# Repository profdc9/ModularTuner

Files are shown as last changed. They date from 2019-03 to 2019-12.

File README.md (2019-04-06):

This a project to create a Modular Antenna Tuner System that can be reconfigured for
different needs.  This material is copyrighted by Daniel Marks (KW4TI) and licensed under
the Creative Commons License CC-BY-SA 4.0.

This project is a toolkit for making automatic antenna tuners and smart HF antennas.

A description and documentation of this project may be found in the "doc" directory as
ModularTuner-Guide.pdf.

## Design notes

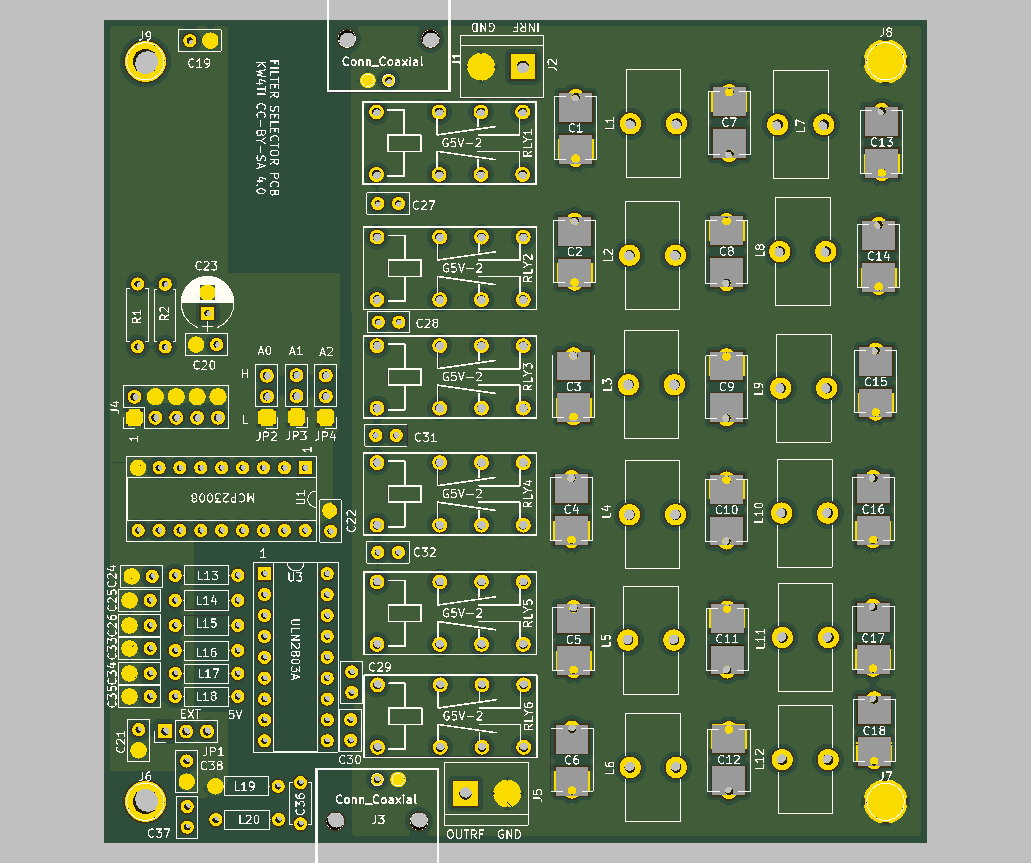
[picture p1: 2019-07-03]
Tuner/Filter/Filter.png

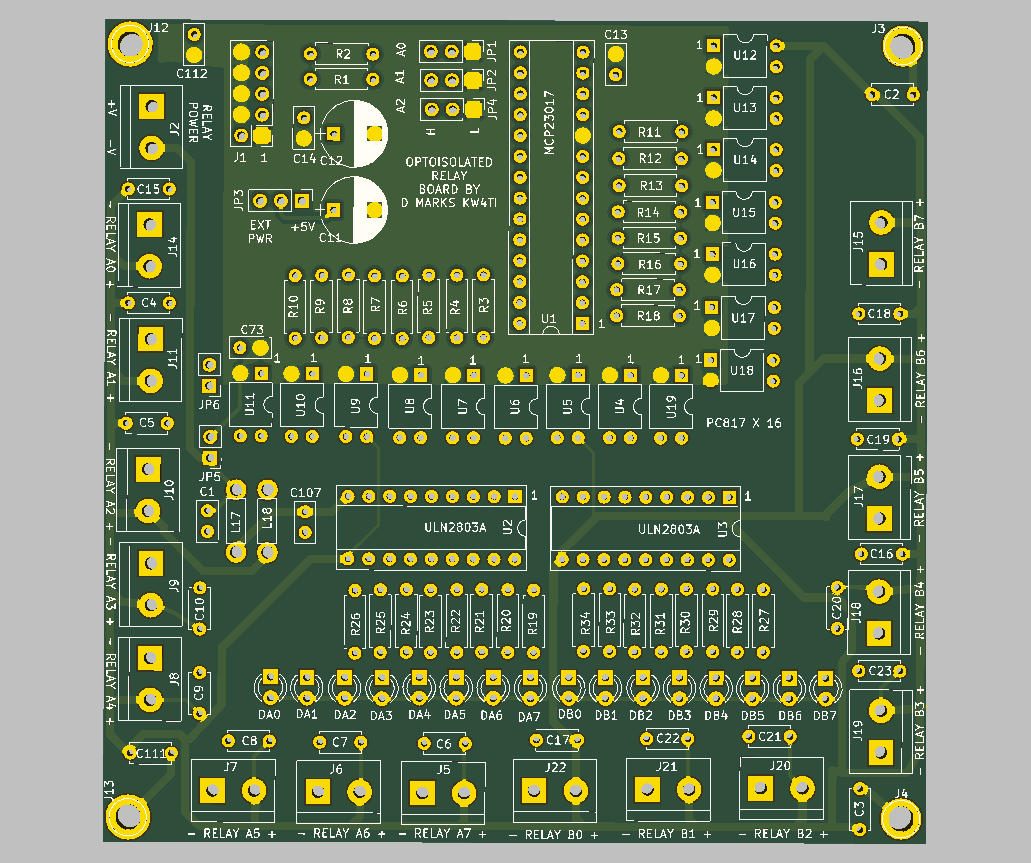
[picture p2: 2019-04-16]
Tuner/OptoisolatedRelay/OptoisolatedRelay.png

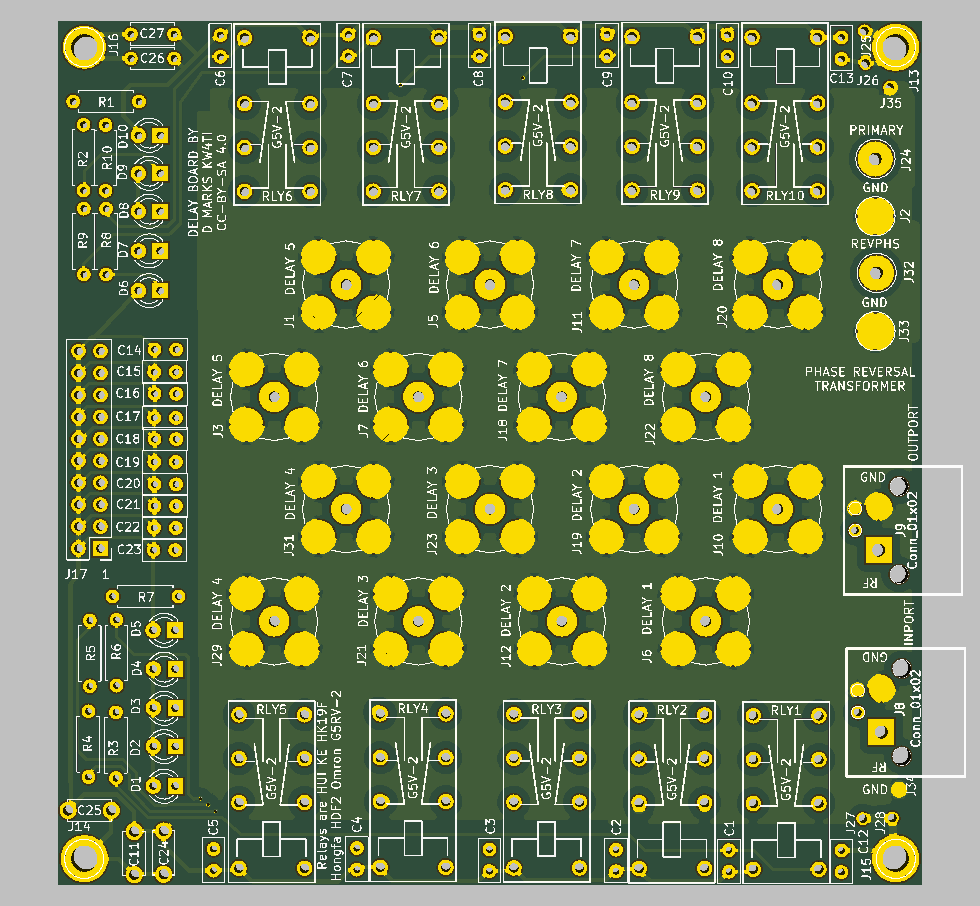
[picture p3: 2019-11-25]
Tuner/DelayLine/DelayLine.png

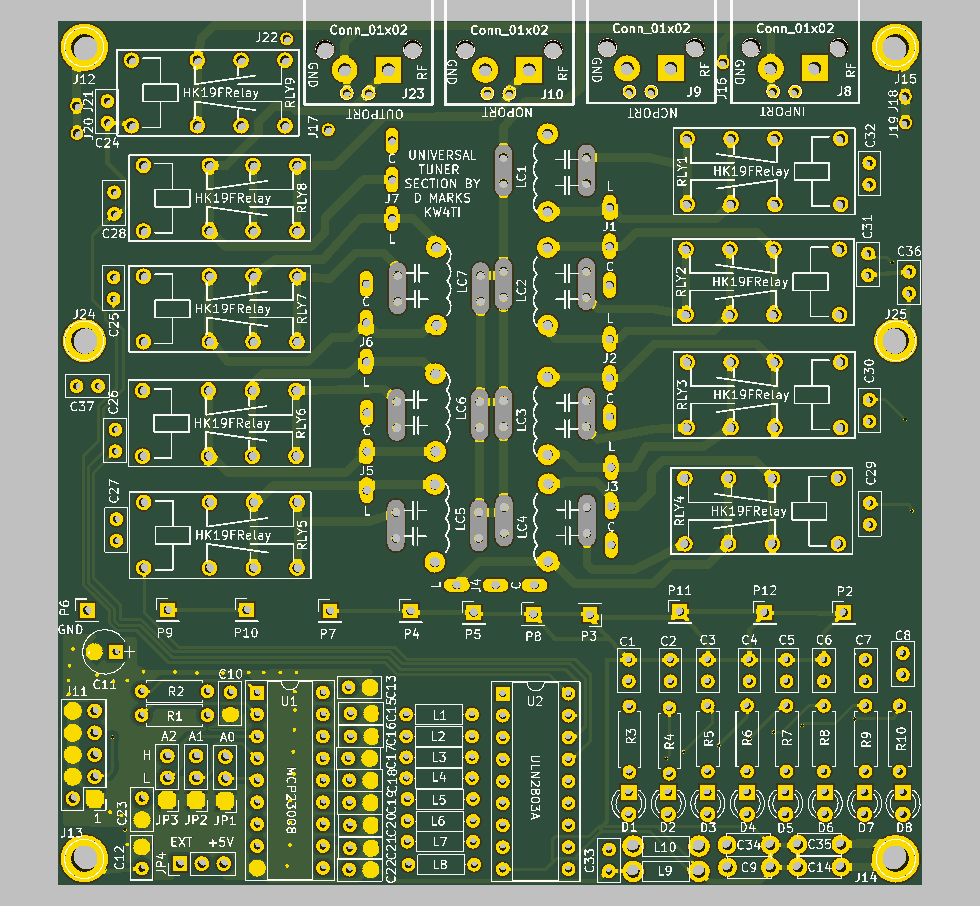
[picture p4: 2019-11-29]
Tuner/ReversibleLittleSection/ReversibleSection.png

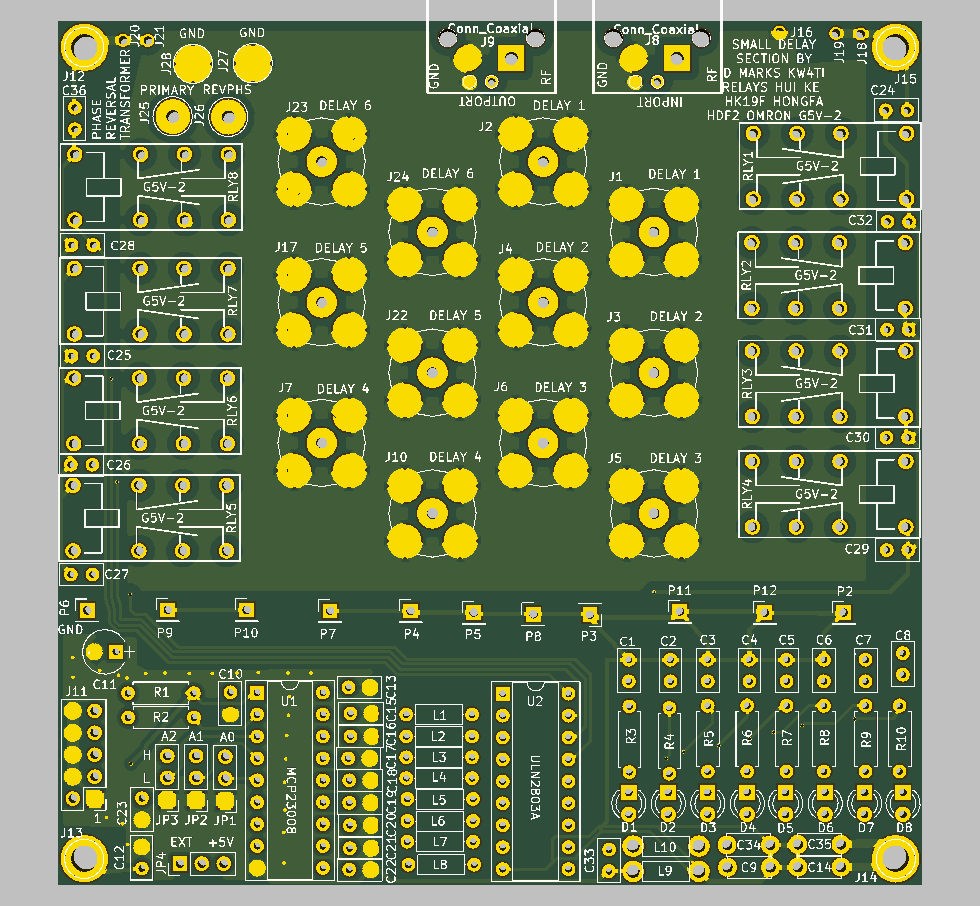
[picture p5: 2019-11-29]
Tuner/LittleDelayLine/LittleDelayLine.png

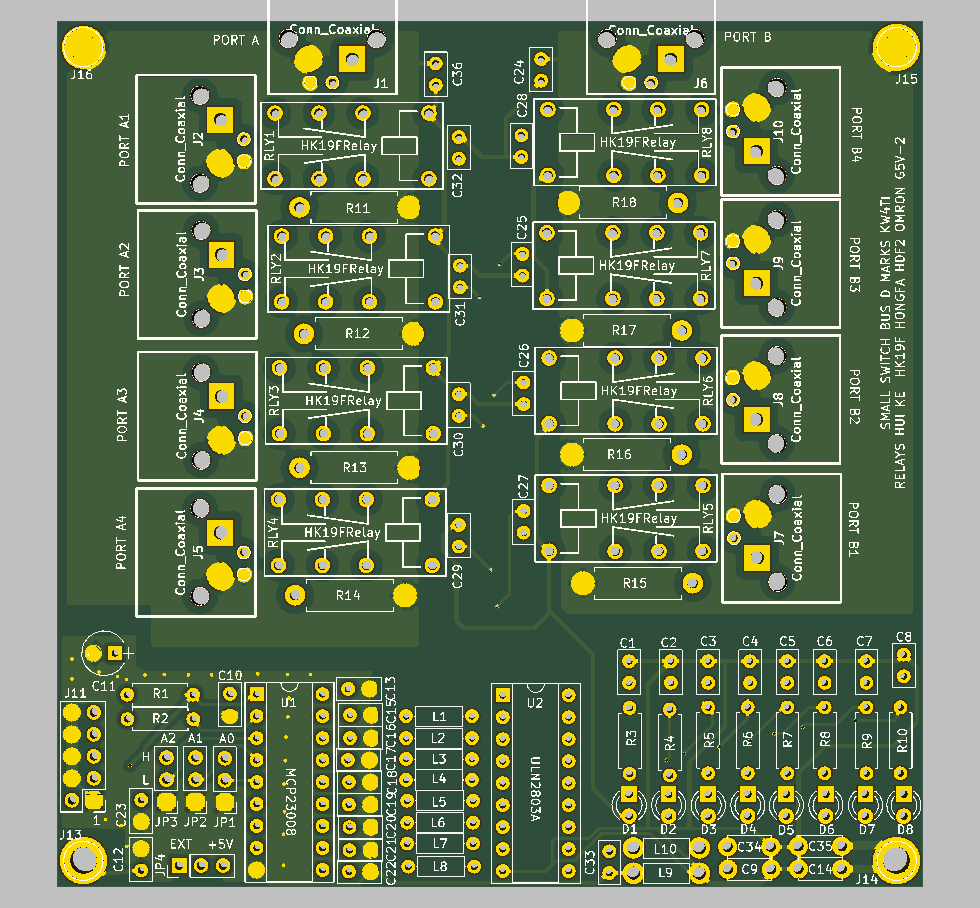
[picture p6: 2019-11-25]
Tuner/LittleSwitchBus/LittleSwitchBus.png

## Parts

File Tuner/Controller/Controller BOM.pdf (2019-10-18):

Controller

Controller Bill Of Materials

Ref | Value
C1 | 100 nF 50 V ceramic disc capacitor
C2 | 100 nF 50 V ceramic disc capacitor
C3 | 100 nF 50 V ceramic disc capacitor
C4 | 1000 uF 10 V electrolytic polarized capacitor
C5 | 100 nF 50 V ceramic disc capacitor
C6 | 100 uF 25 V electrolytic polarized capacitor
C7 | 100 nF 50 V ceramic disc capacitor
C8 | 10 nF 50 V ceramic disc capacitor
C9 | 10 nF 50 V ceramic disc capacitor
C10 | 10 nF 50 V ceramic disc capacitor
C11 | 10 nF 50 V ceramic disc capacitor
C12 | 10 nF 50 V ceramic disc capacitor
C13 | 10 nF 50 V ceramic disc capacitor
C14 | 10 nF 50 V ceramic disc capacitor
C15 | 100 nF 50 V ceramic disc capacitor
C16 | 100 nF 50 V ceramic disc capacitor
C17 | 100 nF 50 V ceramic disc capacitor
C18 | 10 nF 50 V ceramic disc capacitor
C19 | 100 nF 50 V ceramic disc capacitor
C20 | 100 nF 50 V ceramic disc capacitor
C21 | 100 nF 50 V ceramic disc capacitor
C22 | 10 nF 50 V ceramic disc capacitor
C23 | 10 nF 50 V ceramic disc capacitor
C24 | 10 nF 50 V ceramic disc capacitor
C25 | 100 nF 50 V ceramic disc capacitor
C26 | 100 nF 50 V ceramic disc capacitor
C27 | 10 nF 50 V ceramic disc capacitor
C28 | NC
C29 | NC
C30 | 100 nF 50 V ceramic disc capacitor
C31 | 100 nF 50 V ceramic disc capacitor
C32 | 100 nF 50 V ceramic disc capacitor
C33 | 100 nF 50 V ceramic disc capacitor
C34 | 100 nF 50 V ceramic disc capacitor
C35 | 100 nF 50 V ceramic disc capacitor
C36 | 100 uF 25 V electrolytic polarized capacitor
C37 | 100 nF 50 V ceramic disc capacitor
C38 | 100 nF 50 V ceramic disc capacitor
C39 | 100 nF 50 V ceramic disc capacitor
C40 | 100 nF 50 V ceramic disc capacitor
C41 | 100 nF 50 V ceramic disc capacitor
C42 | 100 nF 50 V ceramic disc capacitor
C43 | 10 nF 50 V ceramic disc capacitor
C44 | 10 nF 50 V ceramic disc capacitor

C45 | 10 nF 50 V ceramic disc capacitor
C46 | 100 nF 50 V ceramic disc capacitor
D1 | 1N4004
D2 | 1N4004
D3 | 1N5711 or “ebay 1N60P”
D4 | 1N5711 or “ebay 1N60P”
D5 | 1N5711 or “ebay 1N60P”
D6 | 1N5711 or “ebay 1N60P”
D7 | 1N5711 or “ebay 1N60P”
D8 | 3 mm LED
D9 | 1N5711 or “ebay 1N60P”
D10 | 1N5711 or “ebay 1N60P”
D11 | 1N5711 or “ebay 1N60P”
D12 | 1N5819
D13 | 1N4148
D14 | 1N5819
D15 | 1N4148
D16 | 1N4148
D17 | 1N5711 or “ebay 1N60P”
D18 | 1N4148
D19 | 1N4148
D20 | 1N4148
D21 | 1N4729A
D24 | 1N5819
D25 | 1N5819
D27 | 1N4733A
D28 | 1N4733A
J1 | 2 rows of 5 pin headers 2.54 mm spacing
J2 | 2 rows of 5 pin headers 2.54 mm spacing
J3 | 2 rows of 5 pin headers 2.54 mm spacing
J4 | 2 rows of 5 pin headers 2.54 mm spacing
J5 | 2 rows of 5 pin headers 2.54 mm spacing
J6 | 2 position 5.08 mm screw terminal block
J7 | 2 rows of 5 pin headers 2.54 mm spacing
J8 | 1 rows of 6 pin headers 2.54 mm spacing
J9 | 2 position 5.08 mm screw terminal block or right-angle BNC isolated PCB receptacle
J10 | 1 rows of 5 pin headers 2.54 mm spacing
J11 | 2 position 5.08 mm screw terminal block or right-angle BNC isolated PCB receptacle
J13 | 2 position 5.08 mm screw terminal block or right-angle BNC isolated PCB receptacle
J15 | 2 position 5.08 mm screw terminal block
J16 | JST 2.54 mm male pin socket, 7 pins, 2.54 mm spacing
JP1 | 1 rows of 3 pin headers 2.54 mm spacing
Q1 | 2N3904
Q2 | 2N3904
Q3 | 2N3904
Q4 | 2N3904
Q5 | 2N3904
Q6 | 2N3904
Q7 | 2N3904

Page

3

Q8 | 2N3904
Q9 | 2N7000
Q10 | 2N7000
Q11 | 2N7000
Q12 | 2N7000
R1 | 10k ¼ watt resistor
R2 | 10k ¼ watt resistor
R3 | 1k ¼ watt resistor
R4 | 330R ¼ watt resistor
R5 | 470R ¼ watt resistor
R6 | 10k ¼ watt resistor
R7 | 51R ¼ watt resistor
R8 | 10k ¼ watt resistor
R9 | 10k ¼ watt resistor
R10 | 1k ¼ watt resistor
R11 | 330R ¼ watt resistor
R12 | 1k ¼ watt resistor
R13 | 330R ¼ watt resistor
R14 | 10k ¼ watt resistor
R15 | 1k ¼ watt resistor
R16 | NC
R17 | NC
R18 | 10k ¼ watt resistor
R19 | 100R ¼ watt resistor
R20 | 22k ¼ watt resistor
R21 | 220R ¼ watt resistor
R22 | 220R ¼ watt resistor
R23 | 51R ¼ watt resistor
R24 | 1k ¼ watt resistor
R25 | 1k ¼ watt resistor
R26 | 1k ¼ watt resistor
R27 | 51R ¼ watt resistor
R28 | 220R ¼ watt resistor
R29 | 1k ¼ watt resistor
R30 | 1k ¼ watt resistor
R31 | 1k ¼ watt resistor
R32 | 100R ¼ watt resistor
R33 | 1k ¼ watt resistor
R34 | NC
R35 | 10k ¼ watt resistor
R36 | 1k ¼ watt resistor
R37 | 1.5k ¼ watt resistor
R38 | 1.5k ¼ watt resistor
R39 | 1k ¼ watt resistor
R40 | 1k ¼ watt resistor
R41 | 220R ¼ watt resistor
R42 | 100R ¼ watt resistor
R43 | 1.5k ¼ watt resistor
R44 | 1.5k ¼ watt resistor

R45 | 56R 1 watt resistor
R46 | 1k ¼ watt resistor
R47 | 22k ¼ watt resistor
R48 | 100R ¼ watt resistor
R49 | 220R ¼ watt resistor
R50 | short circuit wire
R51 | 22k ¼ watt resistor
R52 | 220R ¼ watt resistor
R53 | short circuit wire
R54 | 10k ¼ watt resistor
R55 | short circuit wire
R56 | 1k ¼ watt resistor
R57 | 1k ¼ watt resistor
R58 | 1k ¼ watt resistor
R59 | 1.5k ¼ watt resistor
R60 | 1.5k ¼ watt resistor
R61 | 1.5k ¼ watt resistor
R62 | 220R ¼ watt resistor
R63 | 10k ¼ watt resistor
R64 | 56R 1 watt
R65 | 56R 1 watt
R66 | 10k ¼ watt resistor
R67 | 10k ¼ watt resistor
R68 | 10k ¼ watt resistor
R69 | 10k ¼ watt resistor
R70 | 10k ¼ watt resistor
R71 | 10k ¼ watt resistor
R72 | 10k ¼ watt resistor
R73 | 10k ¼ watt resistor
U1 | 74HC393 DIP-14
U2 | 74HC14 DIP-14
U3 | 74HC86 DIP-14
U4 | LM350 TO-220
UB1 | BLUEPILL: solder two 20 pin header sockets into board
| and 20 pin headers on Bluepill, slot into the sockets.

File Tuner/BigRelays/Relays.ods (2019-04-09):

 | E:/ModularTuner/Tuner/BigRelays/Relays.sch
Ref | Value
C1 | 10 nF 50 V ceramic disc capacitor
C2 | 10 nF 50 V ceramic disc capacitor
C3 | 10 nF 50 V ceramic disc capacitor
C4 | 10 nF 50 V ceramic disc capacitor
C5 | 10 nF 50 V ceramic disc capacitor
C6 | 10 nF 50 V ceramic disc capacitor
C7 | 10 nF 50 V ceramic disc capacitor
C8 | 10 nF 50 V ceramic disc capacitor
C9 | 10 nF 50 V ceramic disc capacitor
C10 | 10 nF 50 V ceramic disc capacitor
C11 | 2200 pF to 10 nF 630 V ceramic disc capacitor
C12 | 10 nF 50 V ceramic disc capacitor
C13 | 10 nF 50 V ceramic disc capacitor
C14 | 10 nF 50 V ceramic disc capacitor
C15 | 10 nF 50 V ceramic disc capacitor
C16 | 10 nF 50 V ceramic disc capacitor
C17 | 10 nF 50 V ceramic disc capacitor
C18 | 10 nF 50 V ceramic disc capacitor
C19 | 10 nF 50 V ceramic disc capacitor
C20 | 10 nF 50 V ceramic disc capacitor
C21 | 10 nF 50 V ceramic disc capacitor
C22 | 10 nF 50 V ceramic disc capacitor
C23 | 10 nF 50 V ceramic disc capacitor
C24 | 2200 pF to 10 nF 630 V ceramic disc capacitor
C25 | 2200 pF to 10 nF 630 V ceramic disc capacitor
D1 | 3 mm LED
D2 | 3 mm LED
D3 | 3 mm LED
D4 | 3 mm LED
D5 | 3 mm LED
D6 | 3 mm LED
D7 | 3 mm LED
D8 | 3 mm LED
D9 | 3 mm LED
D10 | 3 mm LED
J8 | 2 position 5.08 mm screw terminal block
J9 | 2 position 5.08 mm screw terminal block
J10 | 2 position 5.08 mm screw terminal block
J11 | 2 position 5.08 mm screw terminal block
J16 | 2 position 5.08 mm screw terminal block
J17 | 2 rows of 10 pin headers 2.54 mm spacing
J18 | 2 position 5.08 mm screw terminal block
J19 | 1 row of 3 pin header 2.54 mm spacing
LC1 | Capacitor or Inductor
LC2 | Capacitor or Inductor
LC3 | Capacitor or Inductor
LC4 | Capacitor or Inductor
LC5 | Capacitor or Inductor
LC6 | Capacitor or Inductor
LC7 | Capacitor or Inductor
LC8 | Capacitor or Inductor
R1 | 1k ¼ watt resistor
R2 | 1k ¼ watt resistor
R3 | 1k ¼ watt resistor
R4 | 1k ¼ watt resistor
R5 | 1k ¼ watt resistor
R6 | 1k ¼ watt resistor
R7 | 1k ¼ watt resistor
R8 | 1k ¼ watt resistor
R9 | 1k ¼ watt resistor
R10 | 1k ¼ watt resistor
RLY1 | “Big” Relay (see documentation)
RLY2 | “Big” Relay (see documentation)
RLY3 | “Big” Relay (see documentation)
RLY4 | “Big” Relay (see documentation)
RLY5 | “Big” Relay (see documentation)
RLY6 | “Big” Relay (see documentation)
RLY7 | “Big” Relay (see documentation)
RLY8 | “Big” Relay (see documentation)
RLY9 | “Big” Relay (see documentation)
RLY10 | “Big” Relay (see documentation)
RLY11 | “Big” Relay (see documentation)
RLY12 | “Big” Relay (see documentation)

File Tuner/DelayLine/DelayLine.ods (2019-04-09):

 | DelayLine Bill of Materials
Ref | Value
C1 | 10 nF 50 V ceramic disc capacitor
C2 | 10 nF 50 V ceramic disc capacitor
C3 | 10 nF 50 V ceramic disc capacitor
C4 | 10 nF 50 V ceramic disc capacitor
C5 | 10 nF 50 V ceramic disc capacitor
C6 | 10 nF 50 V ceramic disc capacitor
C7 | 10 nF 50 V ceramic disc capacitor
C8 | 10 nF 50 V ceramic disc capacitor
C9 | 10 nF 50 V ceramic disc capacitor
C10 | 10 nF 50 V ceramic disc capacitor
C11 | 2200 pF to 10 nF 630 V ceramic disc capacitor
C14 | 10 nF 50 V ceramic disc capacitor
C15 | 10 nF 50 V ceramic disc capacitor
C16 | 10 nF 50 V ceramic disc capacitor
C17 | 10 nF 50 V ceramic disc capacitor
C18 | 10 nF 50 V ceramic disc capacitor
C19 | 10 nF 50 V ceramic disc capacitor
C20 | 10 nF 50 V ceramic disc capacitor
C21 | 10 nF 50 V ceramic disc capacitor
C22 | 10 nF 50 V ceramic disc capacitor
C23 | 10 nF 50 V ceramic disc capacitor
C24 | 2200 pF to 10 nF 630 V ceramic disc capacitor
C25 | 2200 pF to 10 nF 630 V ceramic disc capacitor
D1 | 3 mm LED
D2 | 3 mm LED
D3 | 3 mm LED
D4 | 3 mm LED
D5 | 3 mm LED
D6 | 3 mm LED
D7 | 3 mm LED
D8 | 3 mm LED
D9 | 3 mm LED
D10 | 3 mm LED
J1 | BNC straight female jack PCB mount
J3 | BNC straight female jack PCB mount
J5 | BNC straight female jack PCB mount
J6 | BNC straight female jack PCB mount
J7 | BNC straight female jack PCB mount
J8 | 2 position 5.08 mm screw terminal block or right-angle BNC isolated PCB receptacle
J9 | 2 position 5.08 mm screw terminal block or right-angle BNC isolated PCB receptacle
J10 | BNC straight female jack PCB mount
J11 | BNC straight female jack PCB mount
J12 | BNC straight female jack PCB mount
J17 | 2 rows of 10 pin headers 2.54 mm spacing
J18 | BNC straight female jack PCB mount
J19 | BNC straight female jack PCB mount
J20 | BNC straight female jack PCB mount
J21 | BNC straight female jack PCB mount
J22 | BNC straight female jack PCB mount
J23 | BNC straight female jack PCB mount
J29 | BNC straight female jack PCB mount
J31 | BNC straight female jack PCB mount
R1 | 1k ¼ watt resistor
R2 | 1k ¼ watt resistor
R3 | 1k ¼ watt resistor
R4 | 1k ¼ watt resistor
R5 | 1k ¼ watt resistor
R6 | 1k ¼ watt resistor
R7 | 1k ¼ watt resistor
R8 | 1k ¼ watt resistor
R9 | 1k ¼ watt resistor
R10 | 1k ¼ watt resistor
RLY1 | “Little” relay (see documentation for details)
RLY2 | “Little” relay (see documentation for details)
RLY3 | “Little” relay (see documentation for details)
RLY4 | “Little” relay (see documentation for details)
RLY5 | “Little” relay (see documentation for details)
RLY6 | “Little” relay (see documentation for details)
RLY7 | “Little” relay (see documentation for details)
RLY8 | “Little” relay (see documentation for details)
RLY9 | “Little” relay (see documentation for details)
RLY10 | “Little” relay (see documentation for details)
 | Phase reversal transformer is a common-mode choke
 | Six turns on two stacked FT82-43

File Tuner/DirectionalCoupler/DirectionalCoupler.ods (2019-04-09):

 | DirectionalCoupler Bill of Materials
Ref | Value
 | FT50-43 ferrite toroid with 15 secondary turns of 0.25 to 0.5 mm wire
 | FT50-43 ferrite toroid with 15 secondary turns of 0.25 to 0.5 mm wire
C1 | 10 nF 50 V ceramic disc capacitor
C2 | 10 nF 50 V ceramic disc capacitor
C3 | 10 nF 50 V ceramic disc capacitor
C4 | 10 nF 50 V ceramic disc capacitor
C5 | 10 nF 50 V ceramic disc capacitor
C6 | 10 nF 50 V ceramic disc capacitor
C7 | 10 nF 50 V ceramic disc capacitor
C8 | 10 nF 50 V ceramic disc capacitor
C12 | 10 nF 50 V ceramic disc capacitor
D1 | 1N5711 (or ebay “1N60P”)
D2 | 1N5711 (or ebay “1N60P”)
D3 | 1N4744A
D4 | 1N4004
D5 | 1N4004
D7 | 1N4148
D8 | 1N4148
F1 | Keystone 3544-2 / SL-506P
J1 | 2 position 5.08 mm screw terminal block
J2 | 2 position 5.08 mm screw terminal block
J3 | 2 position 5.08 mm screw terminal block or right-angle BNC isolated PCB receptacle
J4 | 2 position 5.08 mm screw terminal block or right-angle BNC isolated PCB receptacle
J17 | DC Barrel_Jack
J18 | 2 position 5.08 mm screw terminal block or right-angle BNC isolated PCB receptacle
J19 | 2 position 5.08 mm screw terminal block
J20 | 2 position 5.08 mm screw terminal block or right-angle BNC isolated PCB receptacle
J33 | 1 rows of 3 pin headers 2.54 mm spacing
JP1 | 1 rows of 3 pin headers 2.54 mm spacing
JP2 | 1 rows of 2 pin headers 2.54 mm spacing
JP3 | 1 rows of 2 pin headers 2.54 mm spacing
JP4 | 1 rows of 2 pin headers 2.54 mm spacing
JP5 | 1 rows of 2 pin headers 2.54 mm spacing
JP6 | 1 rows of 2 pin headers 2.54 mm spacing
JP7 | 1 rows of 2 pin headers 2.54 mm spacing
JP8 | 1 rows of 2 pin headers 2.54 mm spacing
JP9 | 1 rows of 2 pin headers 2.54 mm spacing
JP12 | 1 rows of 2 pin headers 2.54 mm spacing
L1 | 100 uH RF choke inductor wound around ferrite rod
R1 | 100R 1 watt resistor
R2 | 100R 1 watt resistor
R3 | 100R 1 watt resistor
R4 | 100R 1 watt resistor
R5 | 10k ¼ watt resistor
R6 | 10k ¼ watt resistor
R7 | 10k ¼ watt resistor
R8 | 10k ¼ watt resistor
R21 | 10k ¼ watt resistor
R23 | 1k ¼ watt resistor

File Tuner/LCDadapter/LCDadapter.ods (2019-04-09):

 | LCD adapter Bill of Materials
Ref | Value
C1 | 100 nF 50 V ceramic disc capacitor
C2 | 100 nF 50 V ceramic disc capacitor
C3 | 100 nF 50 V ceramic disc capacitor
C4 | 100 nF 50 V ceramic disc capacitor
C5 | 100 nF 50 V ceramic disc capacitor
C6 | 100 nF 50 V ceramic disc capacitor
D1 | 1N4148
D2 | 1N4148
D3 | 1N4148
D4 | 1N4148
D5 | 1N4148
D6 | 1N4148
J1 | 2 rows of 5 pin headers 2.54 mm spacing
JP1 | 1 rows of 2 pin headers 2.54 mm spacing
JP2 | 1 rows of 2 pin headers 2.54 mm spacing
JP3 | 1 rows of 2 pin headers 2.54 mm spacing
JP4 | 1 rows of 2 pin headers 2.54 mm spacing
Q1 | 2N3904 (OMIT if using buttons!)
R1 | 4.7k ¼ watt resistor
R2 | 4.7k ¼ watt resistor
R6 | 4.7k ¼ watt resistor
R7 | 150R ¼ watt resistor
RV1 | 5k Single Turn Trimmer Potentiometer PCB
SW1 | 4 pin DIP 6 mm micro momentary normally open push button
SW2 | 4 pin DIP 6 mm micro momentary normally open push button
SW3 | 4 pin DIP 6 mm micro momentary normally open push button
SW4 | 4 pin DIP 6 mm micro momentary normally open push button
SW5 | 4 pin DIP 6 mm micro momentary normally open push button
SW6 | 4 pin DIP 6 mm micro momentary normally open push button
U1 | PCF8574 DIP-8
U2 | 1 16 pin header socket, 2.54 mm spacing
 | 1 16 pin header soldered in HD44708 LCD

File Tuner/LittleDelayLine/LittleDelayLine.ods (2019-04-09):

 | Little Delay Line Bill of Materials
 | 115
Ref | Value | Footprint | Datasheet | Manufacturer | Vendor
C1 | 10 nF 50 V ceramic disc capacitor | Capacitors_THT:C_Disc_D5.0mm_W2.5mm_P2.50mm
C2 | 10 nF 50 V ceramic disc capacitor | Capacitors_THT:C_Disc_D5.0mm_W2.5mm_P2.50mm
C3 | 10 nF 50 V ceramic disc capacitor | Capacitors_THT:C_Disc_D5.0mm_W2.5mm_P2.50mm
C4 | 10 nF 50 V ceramic disc capacitor | Capacitors_THT:C_Disc_D5.0mm_W2.5mm_P2.50mm
C5 | 10 nF 50 V ceramic disc capacitor | Capacitors_THT:C_Disc_D5.0mm_W2.5mm_P2.50mm
C6 | 10 nF 50 V ceramic disc capacitor | Capacitors_THT:C_Disc_D5.0mm_W2.5mm_P2.50mm
C7 | 10 nF 50 V ceramic disc capacitor | Capacitors_THT:C_Disc_D5.0mm_W2.5mm_P2.50mm
C8 | 10 nF 50 V ceramic disc capacitor | Capacitors_THT:C_Disc_D5.0mm_W2.5mm_P2.50mm
C9 | 10 nF 50 V ceramic disc capacitor | Capacitors_THT:C_Disc_D5.0mm_W2.5mm_P5.00mm
C10 | 100 nF 50 V ceramic disc capacitor | Capacitors_THT:C_Disc_D5.0mm_W2.5mm_P2.50mm
C11 | 100 uF | Capacitors_THT:CP_Radial_Tantal_D5.0mm_P2.50mm
C12 | 10 nF 50 V ceramic disc capacitor | Capacitors_THT:C_Disc_D5.0mm_W2.5mm_P2.50mm
C13 | 100 nF 50 V ceramic disc capacitor | Capacitors_THT:C_Disc_D5.0mm_W2.5mm_P2.50mm
C14 | 2200 pF to 10 nF 630 V ceramic disc capacitor | Capacitors_THT:C_Disc_D5.0mm_W2.5mm_P5.00mm
C15 | 10 nF 50 V ceramic disc capacitor | Capacitors_THT:C_Disc_D5.0mm_W2.5mm_P2.50mm
C16 | 10 nF 50 V ceramic disc capacitor | Capacitors_THT:C_Disc_D5.0mm_W2.5mm_P2.50mm
C17 | 10 nF 50 V ceramic disc capacitor | Capacitors_THT:C_Disc_D5.0mm_W2.5mm_P2.50mm
C18 | 10 nF 50 V ceramic disc capacitor | Capacitors_THT:C_Disc_D5.0mm_W2.5mm_P2.50mm
C19 | 10 nF 50 V ceramic disc capacitor | Capacitors_THT:C_Disc_D5.0mm_W2.5mm_P2.50mm
C20 | 10 nF 50 V ceramic disc capacitor | Capacitors_THT:C_Disc_D5.0mm_W2.5mm_P2.50mm
C21 | 10 nF 50 V ceramic disc capacitor | Capacitors_THT:C_Disc_D5.0mm_W2.5mm_P2.50mm
C22 | 10 nF 50 V ceramic disc capacitor | Capacitors_THT:C_Disc_D5.0mm_W2.5mm_P2.50mm
C23 | 100 nF 50 V ceramic disc capacitor | Capacitors_THT:C_Disc_D5.0mm_W2.5mm_P2.50mm
C25 | 10 nF 50 V ceramic disc capacitor | Capacitors_THT:C_Disc_D5.0mm_W2.5mm_P2.50mm
C26 | 10 nF 50 V ceramic disc capacitor | Capacitors_THT:C_Disc_D5.0mm_W2.5mm_P2.50mm
C27 | 10 nF 50 V ceramic disc capacitor | Capacitors_THT:C_Disc_D5.0mm_W2.5mm_P2.50mm
C28 | 10 nF 50 V ceramic disc capacitor | Capacitors_THT:C_Disc_D5.0mm_W2.5mm_P2.50mm
C29 | 10 nF 50 V ceramic disc capacitor | Capacitors_THT:C_Disc_D5.0mm_W2.5mm_P2.50mm
C30 | 10 nF 50 V ceramic disc capacitor | Capacitors_THT:C_Disc_D5.0mm_W2.5mm_P2.50mm
C31 | 10 nF 50 V ceramic disc capacitor | Capacitors_THT:C_Disc_D5.0mm_W2.5mm_P2.50mm
C32 | 10 nF 50 V ceramic disc capacitor | Capacitors_THT:C_Disc_D5.0mm_W2.5mm_P2.50mm
C33 | 100 nF 50 V ceramic disc capacitor | Capacitors_THT:C_Disc_D5.0mm_W2.5mm_P2.50mm
C34 | 10 nF 50 V ceramic disc capacitor | Capacitors_THT:C_Disc_D5.0mm_W2.5mm_P5.00mm
C35 | 2200 pF to 10 nF 630 V ceramic disc capacitor | Capacitors_THT:C_Disc_D5.0mm_W2.5mm_P5.00mm
D1 | 3 mm LED | LEDs:LED_D3.0mm
D2 | 3 mm LED | LEDs:LED_D3.0mm
D3 | 3 mm LED | LEDs:LED_D3.0mm
D4 | 3 mm LED | LEDs:LED_D3.0mm
D5 | 3 mm LED | LEDs:LED_D3.0mm
D6 | 3 mm LED | LEDs:LED_D3.0mm
D7 | 3 mm LED | LEDs:LED_D3.0mm
D8 | 3 mm LED | LEDs:LED_D3.0mm
J1 | BNC straight female jack PCB mount | Connectors:bnc-ci
J2 | BNC straight female jack PCB mount | Connectors:bnc-ci
J3 | BNC straight female jack PCB mount | Connectors:bnc-ci
J4 | BNC straight female jack PCB mount | Connectors:bnc-ci
J5 | BNC straight female jack PCB mount | Connectors:bnc-ci
J6 | BNC straight female jack PCB mount | Connectors:bnc-ci
J7 | BNC straight female jack PCB mount | Connectors:bnc-ci
J8 | 2 position 5.08 mm screw terminal block or right-angle BNC isolated PCB receptacle | tuner:bnc_90_1-1337543-0_pad_combo
J9 | 2 position 5.08 mm screw terminal block or right-angle BNC isolated PCB receptacle | tuner:bnc_90_1-1337543-0_pad_combo
J10 | BNC straight female jack PCB mount | Connectors:bnc-ci
J11 | 2 rows of 5 pin headers 2.54 mm spacing | Pin_Headers:Pin_Header_Straight_2x05_Pitch2.54mm
J17 | BNC straight female jack PCB mount | Connectors:bnc-ci
J22 | BNC straight female jack PCB mount | Connectors:bnc-ci
J23 | BNC straight female jack PCB mount | Connectors:bnc-ci
J24 | BNC straight female jack PCB mount | Connectors:bnc-ci
JP1 | 1 rows of 3 pin headers 2.54 mm spacing | Pin_Headers:Pin_Header_Straight_1x03_Pitch2.54mm
JP2 | 1 rows of 3 pin headers 2.54 mm spacing | Pin_Headers:Pin_Header_Straight_1x03_Pitch2.54mm
JP3 | 1 rows of 3 pin headers 2.54 mm spacing | Pin_Headers:Pin_Header_Straight_1x03_Pitch2.54mm
JP4 | 1 rows of 3 pin headers 2.54 mm spacing | Pin_Headers:Pin_Header_Straight_1x03_Pitch2.54mm
L1 | 100 uH axial choke inductor 0.5 W | Inductors_THT:L_Axial_L5.3mm_D2.2mm_P7.62mm_Horizontal_Vishay_IM-1
L2 | 100 uH axial choke inductor 0.5 W | Inductors_THT:L_Axial_L5.3mm_D2.2mm_P7.62mm_Horizontal_Vishay_IM-1
L3 | 100 uH axial choke inductor 0.5 W | Inductors_THT:L_Axial_L5.3mm_D2.2mm_P7.62mm_Horizontal_Vishay_IM-1
L4 | 100 uH axial choke inductor 0.5 W | Inductors_THT:L_Axial_L5.3mm_D2.2mm_P7.62mm_Horizontal_Vishay_IM-1
L5 | 100 uH axial choke inductor 0.5 W | Inductors_THT:L_Axial_L5.3mm_D2.2mm_P7.62mm_Horizontal_Vishay_IM-1
L6 | 100 uH axial choke inductor 0.5 W | Inductors_THT:L_Axial_L5.3mm_D2.2mm_P7.62mm_Horizontal_Vishay_IM-1
L7 | 100 uH axial choke inductor 0.5 W | Inductors_THT:L_Axial_L5.3mm_D2.2mm_P7.62mm_Horizontal_Vishay_IM-1
L8 | 100 uH axial choke inductor 0.5 W | Inductors_THT:L_Axial_L5.3mm_D2.2mm_P7.62mm_Horizontal_Vishay_IM-1
L9 | L9 and L10 are together a common-mode choke | Inductors_THT:L_Axial_L5.3mm_D2.2mm_P7.62mm_Horizontal_Vishay_IM-1
L10 | L9 and L10 are together a common-mode choke | Inductors_THT:L_Axial_L5.3mm_D2.2mm_P7.62mm_Horizontal_Vishay_IM-1
R1 | 10k ¼ watt resistor | Resistors_THT:R_Axial_DIN0207_L6.3mm_D2.5mm_P7.62mm_Horizontal
R2 | 10k ¼ watt resistor | Resistors_THT:R_Axial_DIN0207_L6.3mm_D2.5mm_P7.62mm_Horizontal
R3 | 1k ¼ watt resistor | Resistors_THT:R_Axial_DIN0207_L6.3mm_D2.5mm_P7.62mm_Horizontal
R4 | 1k ¼ watt resistor | Resistors_THT:R_Axial_DIN0207_L6.3mm_D2.5mm_P7.62mm_Horizontal
R5 | 1k ¼ watt resistor | Resistors_THT:R_Axial_DIN0207_L6.3mm_D2.5mm_P7.62mm_Horizontal
R6 | 1k ¼ watt resistor | Resistors_THT:R_Axial_DIN0207_L6.3mm_D2.5mm_P7.62mm_Horizontal
R7 | 1k ¼ watt resistor | Resistors_THT:R_Axial_DIN0207_L6.3mm_D2.5mm_P7.62mm_Horizontal
R8 | 1k ¼ watt resistor | Resistors_THT:R_Axial_DIN0207_L6.3mm_D2.5mm_P7.62mm_Horizontal
R9 | 1k ¼ watt resistor | Resistors_THT:R_Axial_DIN0207_L6.3mm_D2.5mm_P7.62mm_Horizontal
R10 | 1k ¼ watt resistor | Resistors_THT:R_Axial_DIN0207_L6.3mm_D2.5mm_P7.62mm_Horizontal
RLY1 | “Little” relay (see documentation for details) | tuner:G2VRelay
RLY2 | “Little” relay (see documentation for details) | tuner:G2VRelay
RLY3 | “Little” relay (see documentation for details) | tuner:G2VRelay
RLY4 | “Little” relay (see documentation for details) | tuner:G2VRelay
RLY5 | “Little” relay (see documentation for details) | tuner:G2VRelay
RLY6 | “Little” relay (see documentation for details) | tuner:G2VRelay
RLY7 | “Little” relay (see documentation for details) | tuner:G2VRelay
RLY8 | “Little” relay (see documentation for details) | tuner:G2VRelay
U1 | MCP23008 Microchip DIP-18 | Housings_DIP:DIP-18_W7.62mm_Socket
U2 | ULN2803A DIP-18 | Housings_DIP:DIP-18_W7.62mm_Socket
 | Phase reversal transformer is a common-mode choke
 | Six turns on two stacked FT82-43

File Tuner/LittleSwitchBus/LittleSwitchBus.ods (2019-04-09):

 | LittleSwitchBus Bill of Materials
Ref | Value
C1 | 10 nF 50 V ceramic capacitor
C2 | 10 nF 50 V ceramic capacitor
C3 | 10 nF 50 V ceramic capacitor
C4 | 10 nF 50 V ceramic capacitor
C5 | 10 nF 50 V ceramic capacitor
C6 | 10 nF 50 V ceramic capacitor
C7 | 10 nF 50 V ceramic capacitor
C8 | 10 nF 50 V ceramic capacitor
C9 | 10 nF 50 V ceramic capacitor
C10 | 100 nF 50 V ceramic disc capacitor
C11 | 100 uF 10 V electrolytic polarized capacitor
C12 | 10 nF 50 V ceramic capacitor
C13 | 100 nF 50 V ceramic disc capacitor
C14 | 2200 pF to 10 nF 630 V ceramic capacitor
C15 | 10 nF 50 V ceramic capacitor
C16 | 10 nF 50 V ceramic capacitor
C17 | 10 nF 50 V ceramic capacitor
C18 | 10 nF 50 V ceramic capacitor
C19 | 10 nF 50 V ceramic capacitor
C20 | 10 nF 50 V ceramic capacitor
C21 | 10 nF 50 V ceramic capacitor
C22 | 10 nF 50 V ceramic capacitor
C23 | 100 nF 50 V ceramic disc capacitor
C25 | 10 nF 50 V ceramic capacitor
C26 | 10 nF 50 V ceramic capacitor
C27 | 10 nF 50 V ceramic capacitor
C28 | 10 nF 50 V ceramic capacitor
C29 | 10 nF 50 V ceramic capacitor
C30 | 10 nF 50 V ceramic capacitor
C31 | 10 nF 50 V ceramic capacitor
C32 | 10 nF 50 V ceramic capacitor
C33 | 100 nF 50 V ceramic disc capacitor
C34 | 10 nF 50 V ceramic capacitor
C35 | 2200 pF to 10 nF 630 V ceramic capacitor
D1 | 3 mm LED
D2 | 3 mm LED
D3 | 3 mm LED
D4 | 3 mm LED
D5 | 3 mm LED
D6 | 3 mm LED
D7 | 3 mm LED
D8 | 3 mm LED
J1 | 2 position 5.08 mm screw terminal block or right-angle BNC isolated PCB receptacle
J2 | 2 position 5.08 mm screw terminal block or right-angle BNC isolated PCB receptacle
J3 | 2 position 5.08 mm screw terminal block or right-angle BNC isolated PCB receptacle
J4 | 2 position 5.08 mm screw terminal block or right-angle BNC isolated PCB receptacle
J5 | 2 position 5.08 mm screw terminal block or right-angle BNC isolated PCB receptacle
J6 | 2 position 5.08 mm screw terminal block or right-angle BNC isolated PCB receptacle
J7 | 2 position 5.08 mm screw terminal block or right-angle BNC isolated PCB receptacle
J8 | 2 position 5.08 mm screw terminal block or right-angle BNC isolated PCB receptacle
J9 | 2 position 5.08 mm screw terminal block or right-angle BNC isolated PCB receptacle
J10 | 2 position 5.08 mm screw terminal block or right-angle BNC isolated PCB receptacle
J11 | 2 rows of 5 pin headers 2.54 mm spacing
JP1 | 1 rows of 3 pin headers 2.54 mm spacing
JP2 | 1 rows of 3 pin headers 2.54 mm spacing
JP3 | 1 rows of 3 pin headers 2.54 mm spacing
JP4 | 1 rows of 3 pin headers 2.54 mm spacing
L1 | 100 uH axial lead choke inductor
L2 | 100 uH axial lead choke inductor
L3 | 100 uH axial lead choke inductor
L4 | 100 uH axial lead choke inductor
L5 | 100 uH axial lead choke inductor
L6 | 100 uH axial lead choke inductor
L7 | 100 uH axial lead choke inductor
L8 | 100 uH axial lead choke inductor
L9 | L9 and L10 are together a common-mode choke
L10 | L9 and L10 are together a common-mode choke
R1 | 10k ¼ watt resistor
R2 | 10k ¼ watt resistor
R3 | 1k ¼ watt resistor
R4 | 1k ¼ watt resistor
R5 | 1k ¼ watt resistor
R6 | 1k ¼ watt resistor
R7 | 1k ¼ watt resistor
R8 | 1k ¼ watt resistor
R9 | 1k ¼ watt resistor
R10 | 1k ¼ watt resistor
R11 | 51R 1 watt resistor
R12 | 51R 1 watt resistor
R13 | 51R 1 watt resistor
R14 | 51R 1 watt resistor
R15 | 51R 1 watt resistor
R16 | 51R 1 watt resistor
R17 | 51R 1 watt resistor
R18 | 51R 1 watt resistor
RLY1 | “Little” relays (see documentation for details)
RLY2 | “Little” relays (see documentation for details)
RLY3 | “Little” relays (see documentation for details)
RLY4 | “Little” relays (see documentation for details)
RLY5 | “Little” relays (see documentation for details)
RLY6 | “Little” relays (see documentation for details)
RLY7 | “Little” relays (see documentation for details)
RLY8 | “Little” relays (see documentation for details)
U1 | MCP23008 Microchip DIP-18
U2 | ULN2803A DIP-18

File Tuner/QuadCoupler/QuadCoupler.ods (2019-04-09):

 | QuadCoupler Bill of Materials
Ref | Value
C1 | 10 nF 50 V ceramic disc capacitor
C2 | 10 nF 50 V ceramic disc capacitor
C3 | 10 nF 50 V ceramic disc capacitor
C4 | 10 nF 50 V ceramic disc capacitor
C5 | NC
C6 | NC
C7 | NC
C8 | NC
C9 | NC
C10 | NC
C11 | NC
C12 | NC
C13 | NC
C14 | 10 nF 50 V ceramic disc capacitor
C15 | NC
C16 | 2200 pF to 10 nF 630 V ceramic disc capacitor
C17 | 2200 pF to 10 nF 630 V ceramic disc capacitor
C18 | 2200 pF to 10 nF 630 V ceramic disc capacitor
C19 | 10 nF 50 V ceramic disc capacitor
C20 | 2200 pF to 10 nF 630 V ceramic disc capacitor
C21 | NC
C22 | 2200 pF to 10 nF 630 V ceramic disc capacitor
C23 | 2200 pF to 10 nF 630 V ceramic disc capacitor
C24 | 2200 pF to 10 nF 630 V ceramic disc capacitor
C25 | 2200 pF to 10 nF 630 V ceramic disc capacitor
D1 | 1N4148
D2 | 1N4148
D3 | 1N4148
D4 | 1N4148
D5 | 1N4148
D6 | 1N4148
D7 | 1N4148
D8 | 1N4148
J1 | Conn_01x01
J2 | 2 position 5.08 mm screw terminal block or right-angle BNC isolated PCB receptacle
J3 | 2 position 5.08 mm screw terminal block or right-angle BNC isolated PCB receptacle
J4 | 2 position 5.08 mm screw terminal block or right-angle BNC isolated PCB receptacle
J5 | 2 position 5.08 mm screw terminal block or right-angle BNC isolated PCB receptacle
J6 | 2 position 5.08 mm screw terminal block or right-angle BNC isolated PCB receptacle
J10 | 2 position 5.08 mm screw terminal block or right-angle BNC isolated PCB receptacle
J19 | 2 position 5.08 mm screw terminal block or right-angle BNC isolated PCB receptacle
JP1 | 1 rows of 2 pin headers 2.54 mm spacing
JP2 | 1 rows of 2 pin headers 2.54 mm spacing
JP3 | 1 rows of 2 pin headers 2.54 mm spacing
JP4 | 1 rows of 2 pin headers 2.54 mm spacing
JP5 | 1 rows of 2 pin headers 2.54 mm spacing
JP6 | 1 rows of 2 pin headers 2.54 mm spacing
JP7 | 1 rows of 2 pin headers 2.54 mm spacing
JP8 | 1 rows of 2 pin headers 2.54 mm spacing
JP9 | 1 rows of 2 pin headers 2.54 mm spacing
JP10 | 1 rows of 2 pin headers 2.54 mm spacing
R1 | 1k 2 watt resistor
R2 | 1k 2 watt resistor
R3 | 1k 2 watt resistor
R4 | 1k 2 watt resistor
R5 | 1k 2 watt resistor
R6 | 1k 2 watt resistor
R7 | 100k ¼ watt resistor
R8 | 10k ¼ watt resistor
R9 | 1k 2 watt resistor
R10 | 1k 2 watt resistor
R11 | 1k 2 watt resistor
R12 | 1k 2 watt resistor
R13 | 1k 2 watt resistor
R14 | 1k 2 watt resistor
R15 | 10k ¼ watt resistor
R16 | 100k ¼ watt resistor
R17 | 10k ¼ watt resistor
R18 | 100k ¼ watt resistor
R19 | 100k ¼ watt resistor
R20 | 10k ¼ watt resistor
R21 | 1k 2 watt resistor
R22 | 1k 2 watt resistor
R23 | 1k 2 watt resistor
R24 | 1k 2 watt resistor
R25 | 1k 2 watt resistor
R26 | 1k 2 watt resistor
R27 | 1k 2 watt resistor
R28 | 1k 2 watt resistor
R29 | 1k 2 watt resistor
R30 | 1k 2 watt resistor
R31 | 1k 2 watt resistor
R32 | 1k 2 watt resistor
R33 | 1k 2 watt resistor
R34 | 1k 2 watt resistor
R35 | 1k 2 watt resistor
R36 | 1k 2 watt resistor
R37 | 1k 2 watt resistor
R38 | 1k 2 watt resistor
TR1 | autotransformer
TR2 | autotransformer
TR3 | autotransformer
TR4 | autotransformer
TR5 | autotransformer
TR6 | autotransformer
 | TR1,TR3,TR4 are 2 stacked FT82-43 cores
 | TR1 has seven turns wound trifilar (numbers refer winding # and turn #)
 | Turn 1-7 connected to 2-1, 2-7 connected to 3-1
 | Tapped at turns 1-1, 3-1, and 3-6 (turn 3-7 is removed).
 | Ratio of inductances between 1-1/3-6 and 1-1/3-1 should be about 2 to 1 (400:196)
 | TR3 and TR4 have five turns wound trifilar (numbers refer to winding # and turn #)
 | Turn 1-5 connected to 2-1, 2-5 connected to 3-1
 | Tapped at turns 1-1, 2-5, 3-4 (turn 3-5 is removed).
 | Ratio of inductances between 1-1/3-4 and 1-1/2-5 should be about 2 to 1 (196:100)
 | TR2, TR5, TR6 are 2 stacked FT82-43 cores
 | Six turns wound bifilar (numbers refer to winding # and turn #)
 | Turn 1-6 connected to 2-6
 | Tapped at 1-1, 1-6/2-6 and 2-1
 | Inductances between 1-1 to 1-6/2-6 and 1/6-2/6 to 2-1 should be about equal

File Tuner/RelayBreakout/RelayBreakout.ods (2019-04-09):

 | RelayBreakout Bill of Materials
Ref | Value
C1 | 100 nF 50 V ceramic disc capacitor
C2 | 100 nF 50 V ceramic disc capacitor
C3 | 100 nF 50 V ceramic disc capacitor
C4 | 100 nF 50 V ceramic disc capacitor
C5 | 10 nF 50 V ceramic disc capacitor
C6 | 10 nF 50 V ceramic disc capacitor
C7 | 10 nF 50 V ceramic disc capacitor
C8 | 10 nF 50 V ceramic disc capacitor
C9 | 10 nF 50 V ceramic disc capacitor
C10 | 10 nF 50 V ceramic disc capacitor
C11 | 10 nF 50 V ceramic disc capacitor
C12 | 10 nF 50 V ceramic disc capacitor
C13 | 10 nF 50 V ceramic disc capacitor
C14 | 10 nF 50 V ceramic disc capacitor
C15 | 10 nF 50 V ceramic disc capacitor
C16 | 10 nF 50 V ceramic disc capacitor
C17 | 10 nF 50 V ceramic disc capacitor
C18 | 10 nF 50 V ceramic disc capacitor
C19 | 10 nF 50 V ceramic disc capacitor
C20 | 10 nF 50 V ceramic disc capacitor
C21 | 10 nF 50 V ceramic disc capacitor
C22 | 10 nF 50 V ceramic disc capacitor
C23 | 10 nF 50 V ceramic disc capacitor
C24 | 10 nF 50 V ceramic disc capacitor
C25 | 10 nF 50 V ceramic disc capacitor
C26 | 10 nF 50 V ceramic disc capacitor
C27 | 10 nF 50 V ceramic disc capacitor
C28 | 10 nF 50 V ceramic disc capacitor
C29 | 10 nF 50 V ceramic disc capacitor
C30 | 10 nF 50 V ceramic disc capacitor
C31 | 10 nF 50 V ceramic disc capacitor
C32 | 10 nF 50 V ceramic disc capacitor
C33 | 10 nF 50 V ceramic disc capacitor
C34 | 10 nF 50 V ceramic disc capacitor
C35 | 10 nF 50 V ceramic disc capacitor
C36 | 10 nF 50 V ceramic disc capacitor
D1 | 3 mm LED
D2 | 3 mm LED
D3 | 3 mm LED
D4 | 3 mm LED
D5 | 3 mm LED
D6 | 3 mm LED
D7 | 3 mm LED
D8 | 3 mm LED
D9 | 3 mm LED
D10 | 3 mm LED
D11 | 3 mm LED
D12 | 3 mm LED
D13 | 3 mm LED
D14 | 3 mm LED
D15 | 3 mm LED
D16 | 3 mm LED
J5 | 2 rows of 16 pin headers 2.54 mm spacing
 | (may have to use only 14 pins for 14 pin IDC cable)
J6 | 2 position 5.08 mm screw terminal block
J7 | 2 position 5.08 mm screw terminal block
J8 | 2 position 5.08 mm screw terminal block
J9 | 2 position 5.08 mm screw terminal block
J10 | 2 position 5.08 mm screw terminal block
J11 | 2 position 5.08 mm screw terminal block
J12 | 2 position 5.08 mm screw terminal block
J13 | 2 position 5.08 mm screw terminal block
J14 | 2 position 5.08 mm screw terminal block
J15 | 2 position 5.08 mm screw terminal block
J16 | 2 position 5.08 mm screw terminal block
J17 | 2 position 5.08 mm screw terminal block
J18 | 2 position 5.08 mm screw terminal block
J19 | 2 position 5.08 mm screw terminal block
J20 | 2 position 5.08 mm screw terminal block
J21 | 2 position 5.08 mm screw terminal block
L1 | 100 uH axial choke inductor
L2 | 100 uH axial choke inductor
L3 | 100 uH axial choke inductor
L4 | 100 uH axial choke inductor
L5 | 100 uH axial choke inductor
L6 | 100 uH axial choke inductor
L7 | 100 uH axial choke inductor
L8 | 100 uH axial choke inductor
L9 | 100 uH axial choke inductor
L10 | 100 uH axial choke inductor
L11 | 100 uH axial choke inductor
L12 | 100 uH axial choke inductor
L13 | 100 uH axial choke inductor
L14 | 100 uH axial choke inductor
L15 | 100 uH axial choke inductor
L16 | 100 uH axial choke inductor
L17 | 100 uH axial choke inductor
L18 | 100 uH axial choke inductor
L19 | 100 uH axial choke inductor
L20 | 100 uH axial choke inductor
L21 | 100 uH axial choke inductor
L22 | 100 uH axial choke inductor
L23 | 100 uH axial choke inductor
L24 | 100 uH axial choke inductor
L25 | 100 uH axial choke inductor
L26 | 100 uH axial choke inductor
L27 | 100 uH axial choke inductor
L28 | 100 uH axial choke inductor
L29 | 100 uH axial choke inductor
L30 | 100 uH axial choke inductor
L31 | 100 uH axial choke inductor
L32 | 100 uH axial choke inductor
R1 | 1k ¼ watt resistor
R2 | 1k ¼ watt resistor
R3 | 1k ¼ watt resistor
R4 | 1k ¼ watt resistor
R5 | 1k ¼ watt resistor
R6 | 1k ¼ watt resistor
R7 | 1k ¼ watt resistor
R8 | 1k ¼ watt resistor
R9 | 1k ¼ watt resistor
R10 | 1k ¼ watt resistor
R11 | 1k ¼ watt resistor
R12 | 1k ¼ watt resistor
R13 | 1k ¼ watt resistor
R14 | 1k ¼ watt resistor
R15 | 1k ¼ watt resistor
R16 | 1k ¼ watt resistor

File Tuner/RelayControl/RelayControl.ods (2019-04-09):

 | RelayControl Bill of Materials
Ref | Value
C1 | 10 nF 50 V ceramic disc capacitor
C2 | 10 nF 50 V ceramic disc capacitor
C3 | 10 nF 50 V ceramic disc capacitor
C4 | 10 nF 50 V ceramic disc capacitor
C5 | 10 nF 50 V ceramic disc capacitor
C6 | 10 nF 50 V ceramic disc capacitor
C7 | 10 nF 50 V ceramic disc capacitor
C8 | 10 nF 50 V ceramic disc capacitor
C9 | 10 nF 50 V ceramic disc capacitor
C10 | 10 nF 50 V ceramic disc capacitor
C11 | 100 uF 25 V polarized electrolytic capacitor
C12 | 100 uF 25 V polarized electrolytic capacitor
C13 | 100 nF 50 V ceramic disc capacitor
C14 | 100 nF 50 V ceramic disc capacitor
C15 | 10 nF 50 V ceramic disc capacitor
C16 | 10 nF 50 V ceramic disc capacitor
C17 | 10 nF 50 V ceramic disc capacitor
C18 | 10 nF 50 V ceramic disc capacitor
C19 | 10 nF 50 V ceramic disc capacitor
C20 | 10 nF 50 V ceramic disc capacitor
C21 | 10 nF 50 V ceramic disc capacitor
C22 | 10 nF 50 V ceramic disc capacitor
C23 | 10 nF 50 V ceramic disc capacitor
C24 | 10 nF 50 V ceramic disc capacitor
C25 | 10 nF 50 V ceramic disc capacitor
C26 | 10 nF 50 V ceramic disc capacitor
C27 | 10 nF 50 V ceramic disc capacitor
C28 | 10 nF 50 V ceramic disc capacitor
C29 | 10 nF 50 V ceramic disc capacitor
C30 | 10 nF 50 V ceramic disc capacitor
C31 | 10 nF 50 V ceramic disc capacitor
C32 | 10 nF 50 V ceramic disc capacitor
C33 | 10 nF 50 V ceramic disc capacitor
C34 | 10 nF 50 V ceramic disc capacitor
C35 | 10 nF 50 V ceramic disc capacitor
C36 | 10 nF 50 V ceramic disc capacitor
C37 | 10 nF 50 V ceramic disc capacitor
C38 | 10 nF 50 V ceramic disc capacitor
C39 | 10 nF 50 V ceramic disc capacitor
C40 | 10 nF 50 V ceramic disc capacitor
C41 | 10 nF 50 V ceramic disc capacitor
C42 | 10 nF 50 V ceramic disc capacitor
C43 | 10 nF 50 V ceramic disc capacitor
C44 | 10 nF 50 V ceramic disc capacitor
C45 | 10 nF 50 V ceramic disc capacitor
C46 | 10 nF 50 V ceramic disc capacitor
C47 | 10 nF 50 V ceramic disc capacitor
C48 | 10 nF 50 V ceramic disc capacitor
C49 | 10 nF 50 V ceramic disc capacitor
C50 | 10 nF 50 V ceramic disc capacitor
C51 | 10 nF 50 V ceramic disc capacitor
C52 | 10 nF 50 V ceramic disc capacitor
C53 | 100 nF 50 V ceramic disc capacitor
C54 | 100 nF 50 V ceramic disc capacitor
C55 | 100 nF 50 V ceramic disc capacitor
C56 | 100 uF 25 V polarized electrolytic capacitor
C57 | 100 uF 25 V polarized electrolytic capacitor
C58 | 10 nF 50 V ceramic disc capacitor
C59 | 10 nF 50 V ceramic disc capacitor
C60 | 10 nF 50 V ceramic disc capacitor
C61 | 10 nF 50 V ceramic disc capacitor
C62 | 10 nF 50 V ceramic disc capacitor
C63 | 10 nF 50 V ceramic disc capacitor
C64 | 10 nF 50 V ceramic disc capacitor
C65 | 10 nF 50 V ceramic disc capacitor
C66 | 10 nF 50 V ceramic disc capacitor
C67 | 10 nF 50 V ceramic disc capacitor
C68 | 10 nF 50 V ceramic disc capacitor
C69 | 10 nF 50 V ceramic disc capacitor
C70 | 10 nF 50 V ceramic disc capacitor
C71 | 10 nF 50 V ceramic disc capacitor
C72 | 10 nF 50 V ceramic disc capacitor
C73 | 100 nF 50 V ceramic disc capacitor
C74 | 10 nF 50 V ceramic disc capacitor
C75 | 10 nF 50 V ceramic disc capacitor
C76 | 10 nF 50 V ceramic disc capacitor
C77 | 10 nF 50 V ceramic disc capacitor
C78 | 10 nF 50 V ceramic disc capacitor
C79 | 10 nF 50 V ceramic disc capacitor
C80 | 10 nF 50 V ceramic disc capacitor
C81 | 10 nF 50 V ceramic disc capacitor
C82 | 10 nF 50 V ceramic disc capacitor
C83 | 10 nF 50 V ceramic disc capacitor
C84 | 10 nF 50 V ceramic disc capacitor
C85 | 10 nF 50 V ceramic disc capacitor
C86 | 10 nF 50 V ceramic disc capacitor
C87 | 10 nF 50 V ceramic disc capacitor
C88 | 10 nF 50 V ceramic disc capacitor
C89 | 10 nF 50 V ceramic disc capacitor
C90 | 10 nF 50 V ceramic disc capacitor
C91 | 10 nF 50 V ceramic disc capacitor
C92 | 10 nF 50 V ceramic disc capacitor
C93 | 10 nF 50 V ceramic disc capacitor
C94 | 10 nF 50 V ceramic disc capacitor
C95 | 10 nF 50 V ceramic disc capacitor
C96 | 10 nF 50 V ceramic disc capacitor
C97 | 10 nF 50 V ceramic disc capacitor
C98 | 10 nF 50 V ceramic disc capacitor
C99 | 10 nF 50 V ceramic disc capacitor
C100 | 10 nF 50 V ceramic disc capacitor
C101 | 10 nF 50 V ceramic disc capacitor
C102 | 10 nF 50 V ceramic disc capacitor
C103 | 10 nF 50 V ceramic disc capacitor
C104 | 10 nF 50 V ceramic disc capacitor
C105 | 10 nF 50 V ceramic disc capacitor
C106 | 10 nF 50 V ceramic disc capacitor
C107 | 10 nF 50 V ceramic disc capacitor
C108 | 10 nF 50 V ceramic disc capacitor
C109 | 10 nF 50 V ceramic disc capacitor
C110 | 10 nF 50 V ceramic disc capacitor
C111 | 10 nF 50 V ceramic disc capacitor
C112 | 10 nF 50 V ceramic disc capacitor
C113 | 10 nF 50 V ceramic disc capacitor
C114 | 10 nF 50 V ceramic disc capacitor
J1 | 2 rows of 5 pin headers 2.54 mm spacing
J2 | 2 rows of 16 pin headers 2.54 mm spacing
 | In general you populate less, only 10 of the 16 pins of each row
J3 | 2 rows of 5 pin headers 2.54 mm spacing
J8 | 2 rows of 16 pin headers 2.54 mm spacing
 | In general you populate less, only 10 of the 16 pins of each row
JP1 | 1 rows of 3 pin headers 2.54 mm spacing
JP2 | 1 rows of 3 pin headers 2.54 mm spacing
JP3 | 1 rows of 3 pin headers 2.54 mm spacing
JP4 | 1 rows of 3 pin headers 2.54 mm spacing
JP5 | 1 rows of 3 pin headers 2.54 mm spacing
JP6 | 1 rows of 3 pin headers 2.54 mm spacing
JP7 | 1 rows of 3 pin headers 2.54 mm spacing
JP8 | 1 rows of 3 pin headers 2.54 mm spacing
L1 | 100 uH axial choke inductor
L2 | 100 uH axial choke inductor
L3 | 100 uH axial choke inductor
L4 | 100 uH axial choke inductor
L5 | 100 uH axial choke inductor
L6 | 100 uH axial choke inductor
L7 | 100 uH axial choke inductor
L8 | 100 uH axial choke inductor
L9 | 100 uH axial choke inductor
L10 | 100 uH axial choke inductor
L11 | 100 uH axial choke inductor
L12 | 100 uH axial choke inductor
L13 | 100 uH axial choke inductor
L14 | 100 uH axial choke inductor
L15 | 100 uH axial choke inductor
L16 | 100 uH axial choke inductor
L17 | 100 uH axial choke inductor
L18 | 100 uH axial choke inductor
L19 | 100 uH axial choke inductor
L20 | 100 uH axial choke inductor
L21 | 100 uH axial choke inductor
L22 | 100 uH axial choke inductor
L23 | 100 uH axial choke inductor
L24 | 100 uH axial choke inductor
L25 | 100 uH axial choke inductor
L26 | 100 uH axial choke inductor
L27 | 100 uH axial choke inductor
L28 | 100 uH axial choke inductor
L29 | 100 uH axial choke inductor
L30 | 100 uH axial choke inductor
L31 | 100 uH axial choke inductor
L32 | 100 uH axial choke inductor
L33 | 100 uH axial choke inductor
L34 | 100 uH axial choke inductor
L35 | 100 uH axial choke inductor
L36 | 100 uH axial choke inductor
R1 | 10k ¼ watt resistor
R2 | 10k ¼ watt resistor
R3 | 10k ¼ watt resistor
R4 | 10k ¼ watt resistor
U1 | MCP23017 Microchip DIP-28
U2 | ULN2803A DIP-18
U3 | ULN2803A DIP-18
U4 | MCP23017 Microchip DIP-28
U5 | ULN2803A DIP-18
U6 | ULN2803A DIP-18

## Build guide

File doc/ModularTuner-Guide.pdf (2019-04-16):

# ModularTuner Project

## by Daniel Marks, KW4TI

Version 2019-04-06

### Abstract

The ModularTuner project is a collection of PCB modules and software that can be used to experiment with actively tuned antenna designs. It may be used to construct a versatile automatic antenna tuner as a kit to learn about how an antenna tuner works. All of the designs are open source hardware and software to be studied and improved. Because it is modular, the design enables further experimentation with various matching networks, methods of loading antenna elements, and methods of phasing antennas. This project is intended to be educational, inexpensive, and stimulate interest and development of new smart Medium Frequency/High Frequency (1.8-30 MHz) amateur radio antennas.

Project URL:

http://www.github.com/profdc9/ModularTuner

Related projects (not affiliated with this project):

stm32duino project:

http://wiki.stm32duino.com/index.php?title=Main_Page

Installation of stm32duino on Windows:

https://www.stm32duino.com/viewtopic.php?t=32

## Table of Contents

# Introduction

Antennas designed for the medium/high frequency (MF/HF) bands (1.8 to 30 MHz amateur radio bands) have not seen innovations that have occurred for UHF and microwave communications. Because the wavelengths are comparatively large, there are usually few options for antennas as the antenna choices are often dictated by space or site limitations. Unfortunately, few have the space or resources available to deploy phased array antennas in the HF, and even these phased arrays are typically limited to a single band and a few selected radiation patterns. Wireless networks are now extremely agile and accommodate a large number of simultaneous communications channels, frequency bands, and directed beams. HF antennas need to evolve in the 21st century and incorporate technologies that allow adaptation to the communications environment. This project intends to be a toolkit for those who wish to experiment with new antenna designs that can incorporate active sensing and control of the antenna state. It also is a means to construct a simple antenna tuner, such as the L-match tuner documented here, as an educational project.

Automatic antenna tuners were greatly enhanced by the introduction of microprocessors in the 1970s and 1980s. These devices integrate the essentials of adaptive antenna control: tunable elements under automatic control, RF sensing in the form of a reflection bridge, and programming that implements feedback as to minimize the reflections from the load. Microprocessor control enabled advanced forms of feedback not easily achieved by servo mechanisms. These tuners are typically single units with all of these parts integrated together and while they are adaptable to a degree, being able to match a range of loads, their function is usually separate from the antenna. The separation of the designs of the antenna and the matching network is a missed opportunity to achieve active control of the individual parts of the antenna or antenna network which may be used to more easily realize an increased frequency range, gain, and adapt the antenna to the environment. Current antenna designs require large booms and rotators, as in Yagi antennas, or large areas dedicated to antenna arrays. The large size of HF antennas presents a challenge, but active sensing and control of the antenna elements can help overcome some of the difficulties to employing ubiquitous HF antenna networks.

This project breaks out the parts of an automatic antenna tuner into components that may be used to experiment with HF antenna concepts that contain actively controlled elements. It consists of

- A controller module which can sense the forward and reflected power in the load, as well as the current in an antenna element. Equally importantly, it can measure the phase of the reflected signal as well as the antenna current.
- A directional coupler module for sampling the power. This module also includes a bias-tee for powering the device over coaxial cable.
- Modules with switchable series inductors and parallel capacitors to form matching and loading networks on antenna elements.
- Modules to implement variable delays for phasing elements by varying the total length of coaxial cable added to the signal path.
- Modules are controlled using a shielded two-wire communications (I2C) bus.
- For QRO use, there are versions of the modules that separate the relay power control and RF signals on separate PCBs to better isolate the microcontroller from the RF.

- Communications with the controller module with a medium-range ISM wireless modem.
- An optional LCD and pushbutton interface for user interface control.
- A four-way Wilkinson divider for distribution of power to a network of four antennas.
- A switched bus multiplexer than may be used as an antenna selector.

Currently, up to 8 modules can be used simultaneously, only limited by the number of separate I2C addresses that may be independently configured and the fanout of the bus. The software enables configuration of the modules so that component values may be specified that correspond to each switched relay.

Equally importantly, these components are all open hardware and software. The hardware is licensed under the Creative Commons Attribution Share-Alike (CC-BY-SA 4.0) license, and the PCBs are designed in KiCad, an open-source PCB design program. The software is licensed under the zlib license, which is a commercial-use license similar to the MIT license.

In designing these modules, generic electrical components were preferred over more specialized devices when possible, so that the design is less likely to be obsoleted by the unavailability of a component. The STM32F103CBT6 processor is used for the main controller. The PCB used, also called the “Bluepill,” is an extremely low cost, widely available ARM Cortex-M3 processor by STMicroelectronics. It is used in a very large number of devices, like the ATMega328P used for the Arduino, and therefore is not likely to be out of production soon. The Bluepill has Arduino IDE support through the stm32duino project, which is an adaptation of the Arduino libraries to the STM32 Cortex microcontrollers.

Except for the STM32 processor, and the Microchip MCP23008 and MCP23017 I2C peripheral interfaces, the other components are largely generic 74-series logic, diodes, and transistors. Most of the generic components used in the design may be sourced on ebay or aliexpress at a low cost. The PCBs are designed to be a maximum of 10 cm by 10 cm and two layers, and therefore may be fabricated for a very low cost by JLCPCB, Seeedstudio, or other PCB prototyping services. Because of this, this design is hopefully somewhat future-proofed and will be useful for years to come.

I hope that the ModularTuner system helps stimulate new ideas in antenna design and help bring some of the revolutions of wireless communications to the HF band.

# Specifications

- For use at 1.8 MHz to 30 MHz amateur radio bands.
- Able to sense a minimum 1.1 SWR.
- Given component values to achieve a maximum of 4000 pF capacitance and 20 uH inductance, it is designed to match 1.5 SWR or less on 1.8 MHz to 30 MHz with 10 to 600 ohms load resistance on the 160 m band with a wider range on higher bands.
- Measures the phase of the reflected and antenna current signals to ±5° accuracy from 1.8 MHz to 21 MHz bands, ±20° accuracy from 21 MHz to 30 MHz band when 0.25 W or more reflected power is present.
- Selectable phase delay to 6° accuracy at the 10 m band, achieving a full wave of delay at the 80 m band with 26.4 m of RG-58 cable.
- Allows for 100 watt minimum operation. “Big” relays at 100 watts CW, “Little” relays are 100 watts SSB.

Features:

- Eight modules may be attached. Each of the modules may have 7 or 8 relays of switchable inductors or capacitors, or 6 or 8 switchable coaxial cable delays.
- May be operated remotely, delivering DC power over the coaxial cable, and communicating to the unit through an ISM-band wireless modem.
- A power divider is provided to split power to four antennas.
- LCD button panel for user interface control.
- May be programmed and diagnostics performed over USB or wireless.
- The passive component values may be programmed dynamically and the tuner searches for optimal combinations of passive components to match a particular capacitance or inductance.
- Rig control of ICOM transceivers through an AH-4 tuner interface.
- All software and hardware is open source for easy customization.

# Architecture

The ModularTuner architecture consists of the following components, shown in a typical configuration:

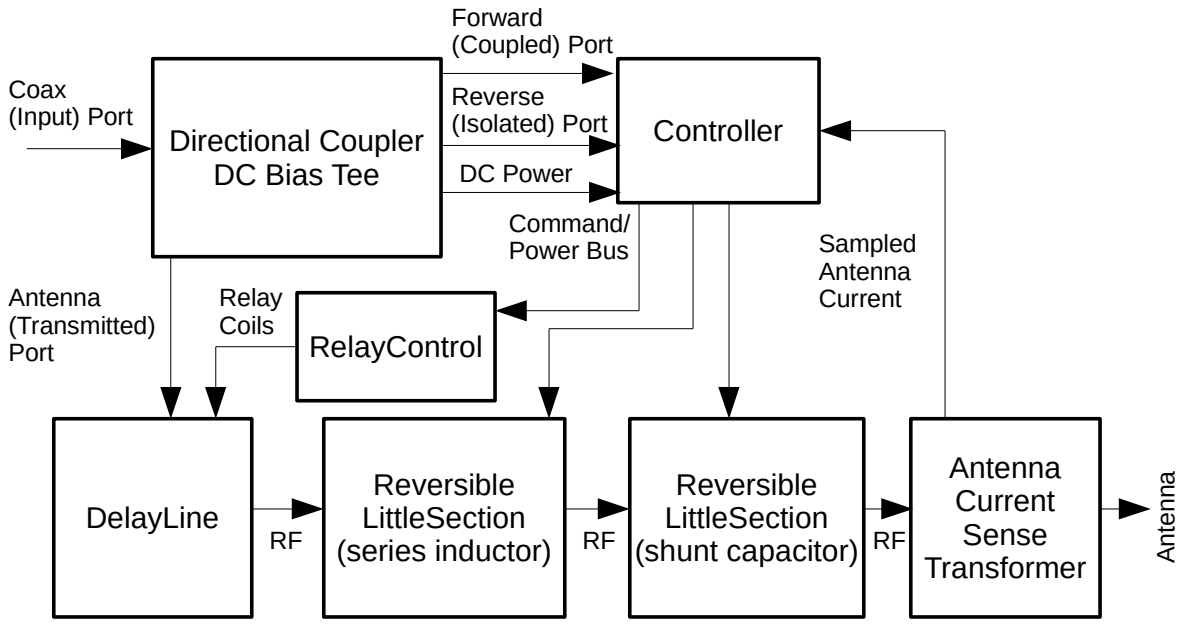
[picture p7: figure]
Directional Coupler; Controller; DC Bias Tee; Forward (Coupled) Port; Reverse (Isolated) Port; Coax (Input) Port; DC Power; Antenna (Transmitted) Port; Reversible LittleSection (series inductor); DelayLine; RelayControl; Command/ Power Bus; Relay Coils; Reversible LittleSection; (shunt capacitor) RF; Sampled Antenna Current; Antenna Current Sense Transformer; Antenna

The Controller contains a microprocessor and circuitry to measure the forward power, reverse power, and the magnitude of the sampled antenna current. In addition, it measures the phase of the reverse signal relative to the forward signal and the phase of the antenna current relative to the forward signal. It has a bus on it that delivers +5V, +12V, and a I2C signal to the modules which connects by a 2-by-5 pin IDC ribbon cable. This controller can have a LCD interface connected to it as well as a ISM-band wireless communications module and a GPS unit.

The Controller obtains a sampled forward and reflected signal from a directional coupler. There is a bias tee integrated with the directional coupler to allow DC power to be delivered over the coaxial cable. Most of the power is conducted through the directional coupler to the transmitted port.

There are three modules that modify the RF signal: a DelayLine, a series inductor ReversibleLittleSection, and a shunt capacitor ReversibleLittleSection.

In this example, there are two modules for the DelayLine. The two module setup (RelayControl and DelayLine) is intended for situations in which extra isolation is required between the Controller and the RF path because the digital and RF path are on separate PCBs, however a LittleDelayLine module could be used where the I2C control circuitry and the relays are on the same PCB if the extra isolation is not required. The RelayControl module receives command signals over I2C and generates a voltage for each relay coil on the DelayLine module. The RelayControl and DelayLine modules are connected by a 2-by-10 pin IDC ribbon cable connector, with one power pin and one pin for each of the 10 relay coils. The DelayLine switches in and out different lengths of coaxial cable to add a variable amount of delay to the RF signal. This delay is sensed as a phase by the antenna current sense transformer at the antenna port.

A “ReversibleLittleSection” configured as series inductors is then in the RF path. This forms part of a L-matching network with the ReversibleLittleSection shunt capacitors. The ReversibleLittleSection, ReversibleBigSection, LittleRelays, and BigRelays can be configured to either switch the elements in either a series or parallel configuration by jumpering particular pads together. In this case, the jumpers are set for series elements, and inductors are soldered into the module. The ReversibleLittleSection has both the circuitry to receive the I2C command signals, generate the relay coil voltages, as well as the relays and the inductors on the same PCB. Therefore a separate RelayControl PCB is not required for a ReversibleLittleSection or ReversibleBigSection.

The section is “reversible” because the RF and ground can be switched between two ports using a pair of relays. One of the ports is the normally closed port and is connected when power is off, and the other is normally open. On the inductor section, the normally closed port may be wired to short out the inductor when power is off so that the inductor board is bypassed. When the inductor board is active, the relay is energized and the section switches to the normally open port and the inductance of the section is in the RF path.

A second ReversibleLittleSection is configured for parallel capacitors. In this case the reversible switch is used to switch the capacitors from a low-Z to a high-Z configuration of the L network, so that the shunt capacitor is placed on one side or the other side of the series inductor. It can be seen that the port switches on the inductor/capacitor boards may be used to reconfigure the topology of a matching network.

Finally, an antenna current sensing transformer samples the antenna current after the matching network. This transformer is connected to the Controller which measures the relative phase of the antenna current and the forward voltage signal. This can be used with the delay section to obtain a particular phase between the forward signal and the radiated signal. This is useful for a phased array antenna as the phase reference is derived from the single forward signal at the transmitter.

# Power/command bus

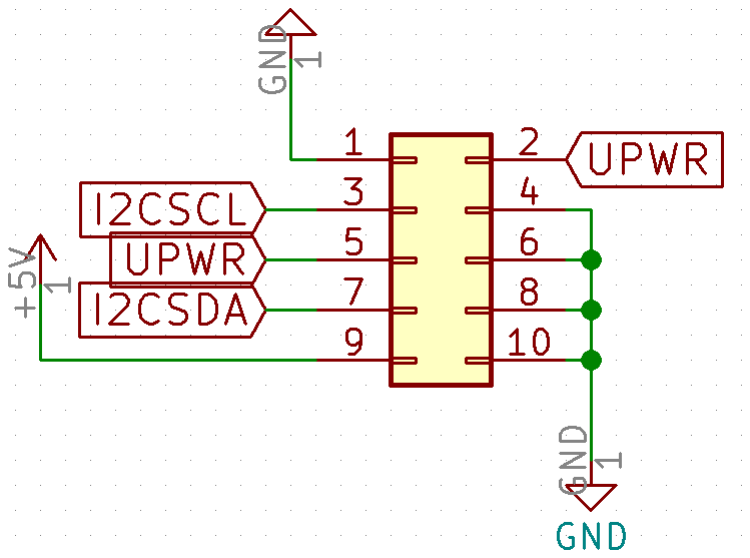
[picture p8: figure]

The pinout of the power/command bus is above. The connector is a 2-by-5 IDC ribbon cable connector with 2.54 mm spacing pins. Pins 1, 4, 6, 8, and 10 are ground. Pin, 9 is +5 VDC. Pins 2 and 5 are +12 VDC but perhaps unregulated, which is used for the relay coils which are not overly sensitive to voltage levels. Pins 3 and 7 are the clock and data lines of the I2C bus. There are power or ground lines between the digital signals to shield these digital signals from RF as they are relatively high impedance connections.

At both ends of the cable, the grounds should be connected together, the two UPWR signals should be connected together and to the ground with a 100 nF capacitor close to the connector, and the +5V should be connected to ground with a 100 nF capacitor also close to the connector, as to prevent any RF potential between the power buses. The DC ground should be connected to the RF ground through a 100 nF capacitor through a metal standoff to the chassis.

# Grounding

One of the most difficult aspects of designing an antenna tuner or antenna system that spans several separate PCBs is maintaining good RF grounding. One of the more challenging aspects of designing the ModularTuner system was to ensure the grounding is thorough as to not allow any paths for the RF to affect sensitive components such as the microcontroller, and conversely to not allow the digital noise of the microcontroller to find its way into the RF path. By following the system set up by these modules, good grounding will be maintained and these problems avoided.

Typically, an antenna tuner is designed inside a single RF grounded, metal enclosure with the PCB itself grounded to the enclosure in many places. There is an intended path for the radio frequency signal, and this path is isolated from digital components by using capacitors to shunt RF energy to the grounded enclosure as well as inductors or RF chokes to provide an increased impedance to the RF to components it should not affect. Ideally, all paths around any RF susceptible components are fenced in by shunt capacitors, series inductors, or ground shields. All of these approaches are used in the ModularTuner.

The simplest approach to grounding is to use a single enclosure or metal sheet as a ground plane. The coaxial connector shields should attach to the enclosure wall or attach with a very short grounding strap to the metal sheet. The modules are intended to be grounded to the enclosure or ground plane through metal standoffs. The standoffs contact the PCB using a widened trace intended to ensure a good contact. These standoffs are capacitively coupled to the power rails in the circuit as to shunt any RF signal in the power supply rails on all of the modules into the RF ground. The modules are designed so that the RF signal from the signal path is blocked by inductors or chokes and the return currents between the RF path and low voltage paths occur mostly through the metal standoffs and the ground plane. Therefore the best way to ensure that good grounding is achieved is to ensure all of the RF coupling capacitors to the standoffs are installed, and that all of the standoffs are installed at the four corners of each module. This is the simplest and most foolproof approach.

Unfortunately, it may not be possible to place everything into the same enclosure and ground it to a single piece of metal. For installing tunable elements that are outside of the enclosure, there are modules that separate the relay control (the RelayControl module) and tunable modules that contain only the tunable elements and relays (the BigRelays, LittleRelays, and DelayLine modules). The ribbon cable connection between the tunable modules and the RelayControl consist only of the power to the relay coils and therefore is relatively insensitive to RF interference. There are capacitors and grounds to reduce any RF signals that may be between the conductors of the cable, however, there is still a common-mode signal because the ribbon cable itself acts as an antenna. Therefore cables that are not grounded that go outside the enclosure, like the ribbon cable to the tunable modules, should have a common-mode choke placed on them. This can be achieved by wrapping the ribbon cable several times around a ferrite toroid, often a FT240-31 or FT240-43 toroid. The toroid should be placed near where the cable enters the RF shielded enclosure. In general, if a connection can not be grounded with a very short connection to the same ground as the enclosure, a ferrite choke should be used to prevent the common-mode signal from entering the enclosure.

# Relays

The relays used for the ModularTuner are two types commonly used for amateur radio projects. Two two types here are called the “Big” and “Little” relays. These two relay types have footprints that separate the pins of the relay coil from the pole as to minimize the capacitance between the two. The capacitance between the poles and the coil of the relay serve as a shunt capacitor to ground, which if sufficiently large, can prevent the load from being matched.

The two types of relays have the following footprints. Metric and imperial near-equivalent dimensions, e.g. 0.2 inch or 5 mm, 0.3 inch or 7.5 mm, etc. can be substituted without problems.

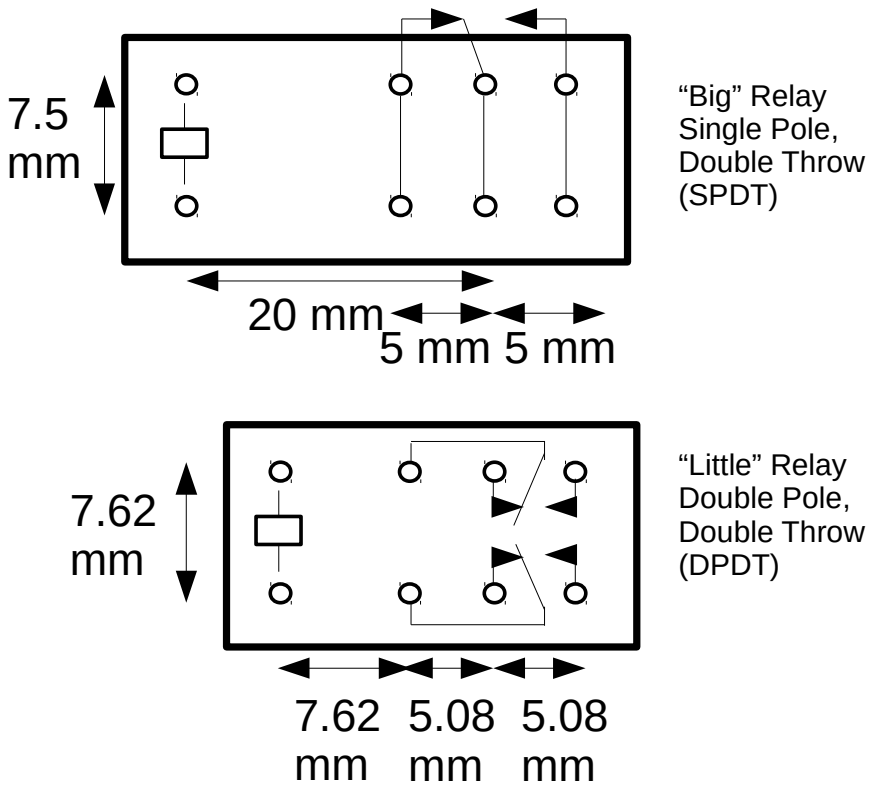
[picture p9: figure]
“Big” Relay Single Pole, Double Throw (SPDT); “Little” Relay Double Pole, Double Throw (DPDT)

Examples of the big-type relays are the Omron G2RL-1, Schrack RTH14012, Songle SMIH-12VDC-SL-C, and Hui Ke HK14F relays. These are single pole, double throw (SPDT) relays that are rated for up 15 to 16 amps (not RF) typically. These types of relays have been used in QRO antenna tuners and have a very low pole-coil capacitance around 1 pF.

Examples of the little-type relays are the Omron G5V-2, Axicom D2N, Hongfa HFD27 relays, and the Hui Ke HK19F relay. These are double pole, double throw (DPDT) signal relays and are good perhaps up to 100 watts. These relays have a pole-coil capacitance per pole of about 2 pF and total of about 4 pF for both poles. Because the relays generally have a lower current capacity, typically around 2 A per pole, these are more susceptible to damage from high power switching. The software is designed to minimize the possibility of hot switching the relays with full power applied by not tuning if excessive power is detected, however, if excessive hot switching occurs, the lifetime of the relays will be greatly reduced.

Unfortunately, not every relay that has these footprints will work as it depends sensitively on how the relay is constructed. If you are using an unknown relay, measuring the pole-coil capacitance with a LCR-meter or a vector network analyzer may help identify if excessive RF energy will leak out of the coil to ground.

# Description of Modules

## Controller Module

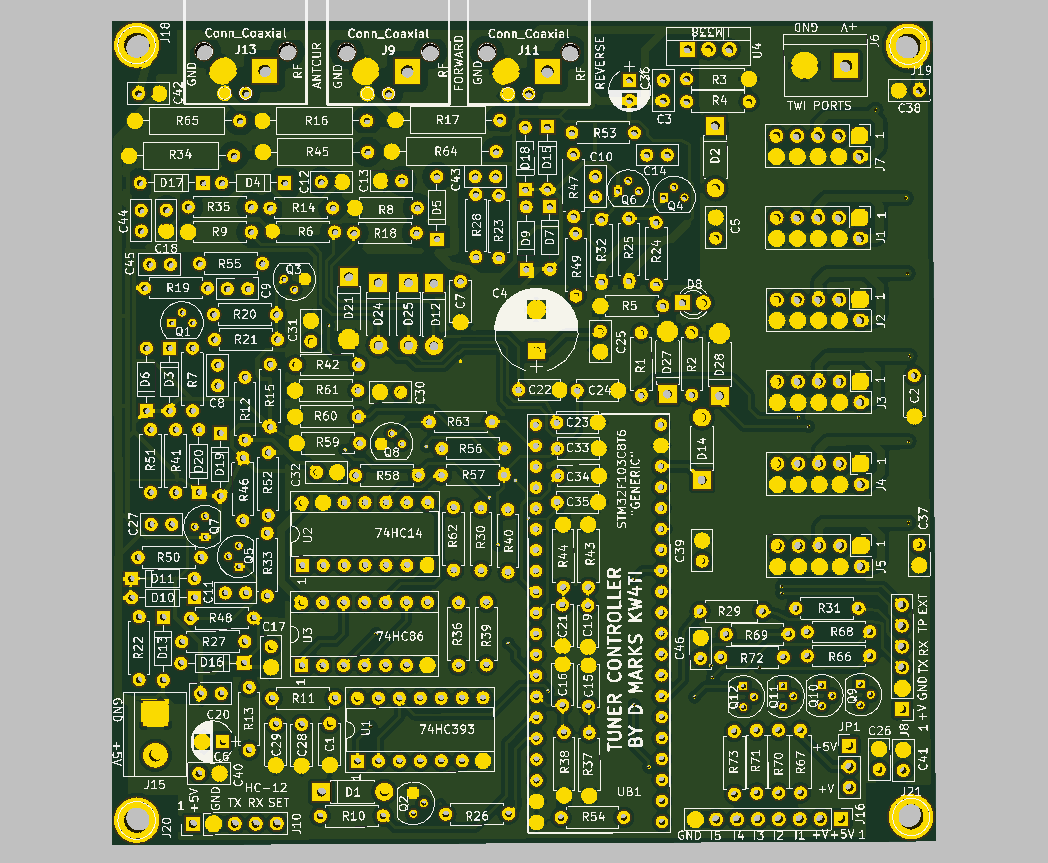
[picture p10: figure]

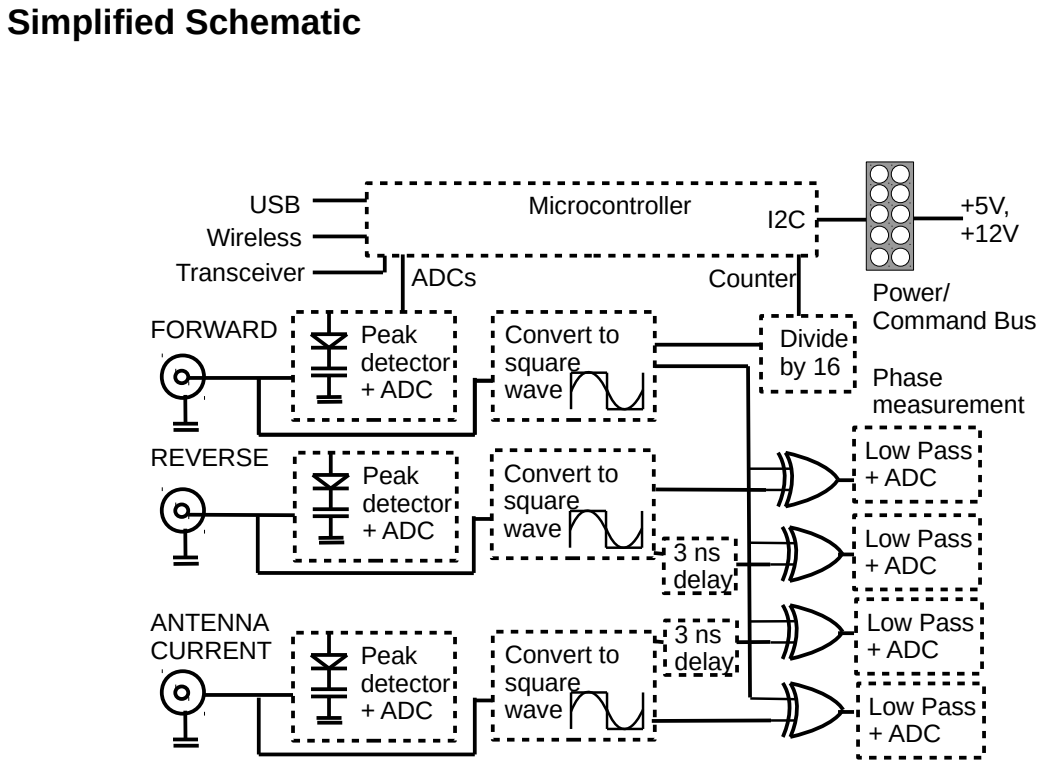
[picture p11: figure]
Simplified Schematic; FORWARD; REVERSE; ANTENNA CURRENT; Peak detector + ADC; Convert to square wave; 3 ns delay; Low Pass + ADC; Microcontroller; ADCs; Divide by 16; Counter; USB Wireless Transceiver; Phase measurement; Power/ Command Bus

The Controller Module contains the microcontroller that senses the state of the antenna system and adjusts the elements accordingly. It is intended to be isolated from the RF path through the two transformers of the Directional Coupler board. It contains the following components:

The silkscreened boxed component in the central lower portion of the PCB is where the STM32F103C8T6 Bluepill board is attached. It is a very inexpensive, readily available Cortex M3 processor running at 72 MHz with 64k/128k of flash (almost all Bluepills contain 128k flash parts currently), 20k of static RAM, ten 12-bit A/D converters, and many other common microcontroller peripherals such as SPI, I2C, and UART ports.

The three connectors at the top of the board from left to right, also in silkscreen boxes, are the input coaxial cable ports for the antenna current transformer, the forward sensed power, and the reverse sensed power from the TandemMatch. The connector footprints can take either a plastic body right-angle PCB BNC panel mount, or a 5.08 mm two position screw terminal block. This combination footprint is used throughout the board to allow either BNC connectorized or bare-ended RG-58 coaxial cables to be used. At the upper right is the power connector for +12V.

There are six power/command bus connectors that connect to modules using 2-by-5 IDC ribbon cables.

At the lower left, there is a 5-pin connector for a HC-12 433 MHz ISM band wireless module for medium-range communication between the shack and the Controller. At the lower right there are two connectors. The connector on the right side of the board is for a NEO 7M GPS module, but it also breaks out the UART1 pins that may be used to program the flash of the Tuner/Controller. Finally on the lower edge of the board on the right, there are several pins that have MOSFET level shifters. These are intended to be connected to transceivers for rig control, for example, to initiate a tuning cycle of the Controller.

There are peak-detector diodes to measure the power in the forward, reverse, and antenna current ports which are sampled by the microcontroller. Furthermore, there is circuitry to measure the relative phase of the forward and reverse signals as well as the forward and antenna current signals. The phase measurement is implemented by transforming the sine wave signals into square waves and then using an exclusive-or gate to produce a signal with a phase proportional to the duty cycle of the square wave. Measuring two relative phases, with one of the signals slightly delayed, disambiguates positive and negative phase. These phases may be used to estimate the complex load impedance of the antenna as well as provide feedback to control the phase of the radiated signal relative to the incoming signal.

On the Bluepill microcontroller board, there is a USB port that is programmed to present a serial port to be connected to a PC. A command-line interface may be accessed through this port to control the ModularTuner through a PC. These commands are documented in a later section. If the ModularTuner is in a remote location, this command-line interface may also be accessed through the HC-12 wireless interface, however, this is a much slower access method.

## DirectionalCoupler Module

Simplified Schematic

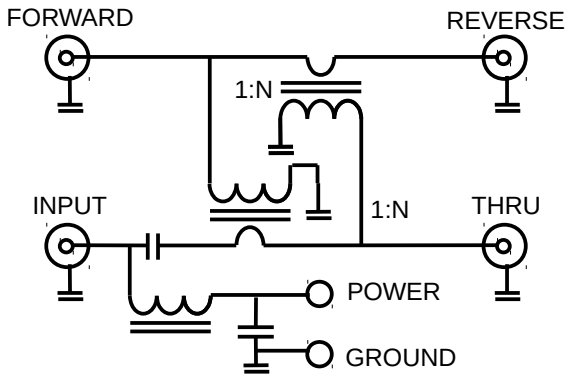
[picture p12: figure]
FORWARD; REVERSE; INPUT; THRU; POWER; GROUND

The DirectionalCoupler module is a directional coupler that supplies samples of the forward and reverse signals to the Controller. It has several diagnostic components that may be jumpered in and out to test the DirectionalCoupler.

Two transformers are used to sample the voltage and current from the input port J20. These transformers are typically FT50-43 ferrite cores with 15 secondary turns for 100 watt operation. The sampled forward signal is at the connector J18, and the sampled reverse signal at J3. Again, the combined footprint ports are present to allow either a connectorized BNC cable or bare-ended RG-58 to be used to connect the boards. The transmitted port is J4.

The following diagnostics are present on the board:

JP3: by closing JP3, the peak voltage on the input port may be sensed at JP4. JP5: by closing JP5, the reverse port may loaded with 50 ohms.
JP6: by closing JP6, the forward port may be loaded with 50 ohms.
JP9: by closing JP9, the peak voltage on the forward port may be sensed at J33.
JP12: by closing JP12, the peak voltage on the reverse port may be sensed at J33.
JP7: by opening JP7, the reverse port coaxial connector may be disconnected so that the 50 ohm load may be connected using JP5.
JP8: by opening JP8, the forward port coaxial connector may be disconnected so that the 50 ohm load may be connected using JP6.

For normal use, JP7 and JP8 should be closed, and JP3, JP5, JP6, JP9, and JP12 should be open.

These jumpered diagnostic connections can help ensure that the DirectionalCoupler is working properly to sample the forward and reflected signal.

There is also a bias-tee on the bottom of the board. A RF choke is placed close to the input port J20 to conduct the DC power on the coaxial cable but block the RF signal. This power is made available at several connector blocks. The power may also be injected through these ports or a barrel connector.

A fuse holder at F1 can hold a SL-506P auto-fuse holder. A 3 A auto fuse should be fitted into the holder.

## RelayControl Module

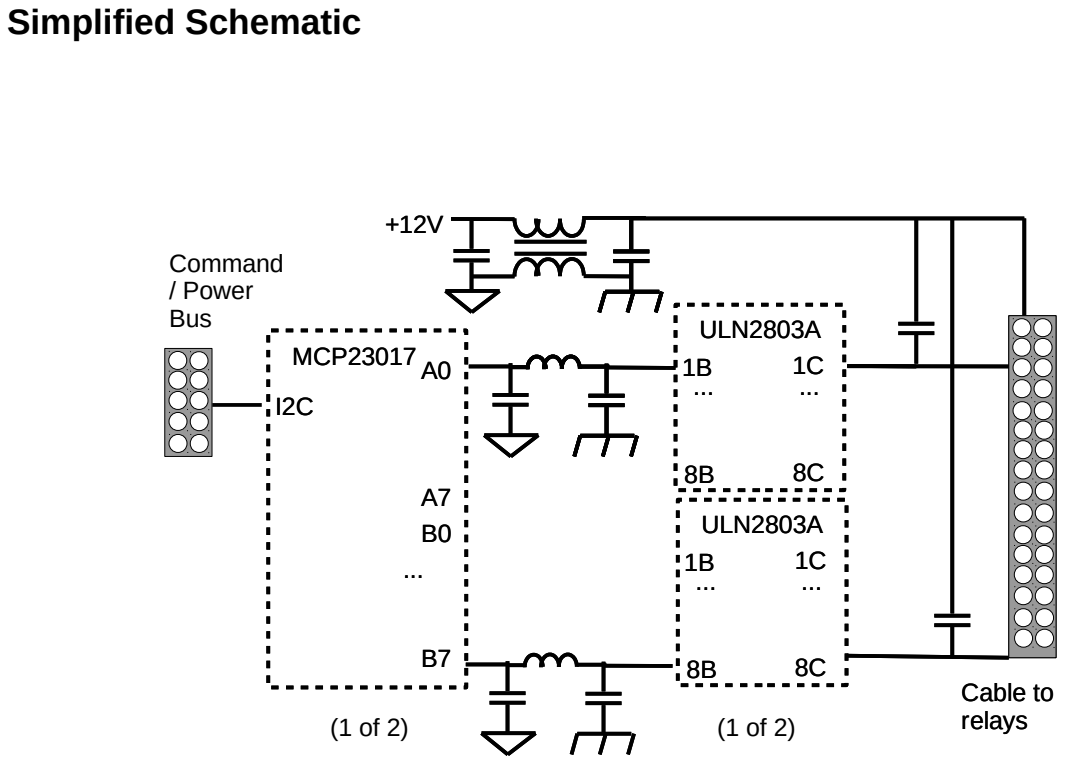
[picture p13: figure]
Simplified Schematic; MCP23017; ULN2803A 1B ...; Command / Power Bus; Cable to relays; Cable to; relays (1 of 2)

The RelayControl module receives I2C commands from the Controller and provides output voltages to control relay coils. On each RelayControl module, there are two Microchip MCP23017 I2C peripherals, each of which can control up to 16 relay coils. Only one of the two connectors J1 and J3 need be connected to the Controller.

This module is intended to isolate the RF path from the digital signals. The left half of the board is the digital portion, while the right half is the relay control portion. Every connection between these two halves have a common-mode choke or inductor in the path. L17/L18 and L35/L36 are common-mode chokes, while L1-L16 and L19-L34 are 100 uH axial inductors. The RF current is blocked from crossing between the two halves of the board by the chokes and inductors and only low frequency return currents cross to provide the slow relay signals. The RF current is returned mainly through the metal standoffs at the four corners of the board. Therefore the standoffs at the four corners should be attached to the chassis.

The jumpers at JP3 and JP7 choose the relay coil voltage either from the +5V supply or the EXT PWR. Almost always, EXT PWR will be used with 12 volt coil voltages to minimize the current carried on the bus cables.

The I2C address for the 16 relays on the top half of the board are selected using the jumpers JP4, JP2, and JP1, while the I2C address for the 16 relays on the bottom half of the board are selected using JP8, JP6, and JP5.

The coil voltages are at the connectors J2 and J8. There is a positive supply pin for each coil and a coil voltage pin that is grounded to energize the coil. The power supply pins on both sides of the ribbon cable connection the RelayControl module and the relay module must be grounded through capacitors on both sides of the ribbon cable, and there should be capacitor between every the power supply pin and the coil voltage pin on every coil. The relay modules designed for ModularTuner ground the power supply pins through the metal standoffs. If it is not possible to ground both sides of the ribbon cable, a common-mode choke should be placed on the cable.

Usually, not all 16 relay coil outputs of each MCP23017 are used. The relay coils that are used start at the 1-pins of the J2 and J8 connectors, so that the first relay coil is connected to pins 1 and 2, the second coil to 3 and 4, etc. Therefore, for example, when controlling 10 relays as in the BigRelays, LittleRelays, and DelayLine boards, pin headers need only be soldered into the first 20 pins of the J2 and J8 connectors, and the other pins 21 to 32 should not be used so that a 2-by-10 IDC ribbon cable will fit over the 20 pin header without interference from the unused pins.

If you are using the RelayControl module to control your own relay board design, it is important to ensure that 10 to 100 nF capacitors are placed across all of the coils of the relays, the positive power rail of the relays are all joined together, and that the relays are all collectively grounded through the positive power rail to the RF chassis ground through another capacitor, usually a 1 kV or higher 10 nF capacitor, or perhaps even several capacitors in parallel to reduce impedance. If the board is large, it may be necessary to ground the relay coils in several places to the chassis to ensure short connections from any relay coil to RF ground. If too much RF energy is transmitted to the RelayControl board and has to be shunted to ground there, it may damage the small capacitors that shunt the RF power at the RelayControl board, as the RelayControl board is designed so that most of the RF power should be shunted to ground near its source. Failing that, a common-mode choke can be placed on the ribbon cable as well.

## RelayBreakout Module

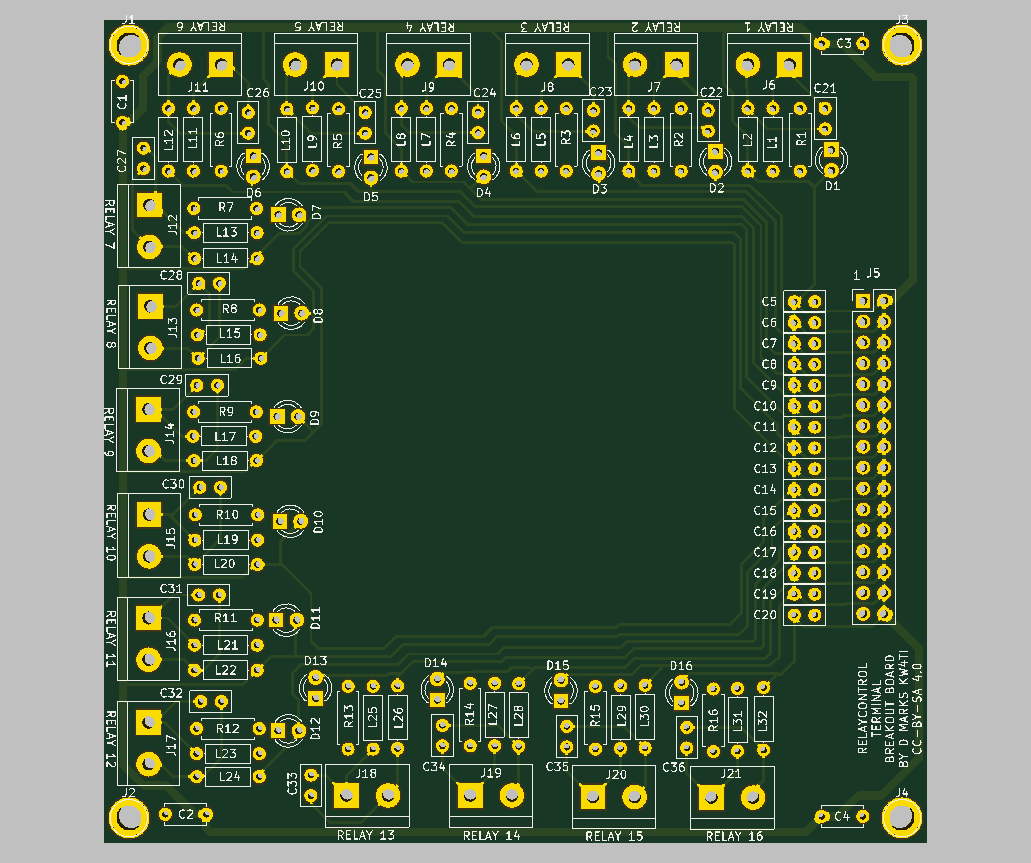
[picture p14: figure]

The RelayBreakout module is a simple module that breaks each of the relay coil terminals into separate screw terminal blocks. It also adds an extra layer of RF isolation because this board contains 100 uH chokes in series with both terminals. It is intended for those who wish to wire their own relays to the RelayControl board, but want the convenience of screw terminals and the extra isolation. It may be used, for example, to switch relays that load parasitic elements on vertical antenna arrays or Yagi antennas. The relays for these applications are likely to have high RF leakage into them and therefore extra isolation is desirable. The remaining RF that passes through the chokes is grounded to the chassis through capacitors at all four corners of the PCB.

## OptoisolatedRelay Module

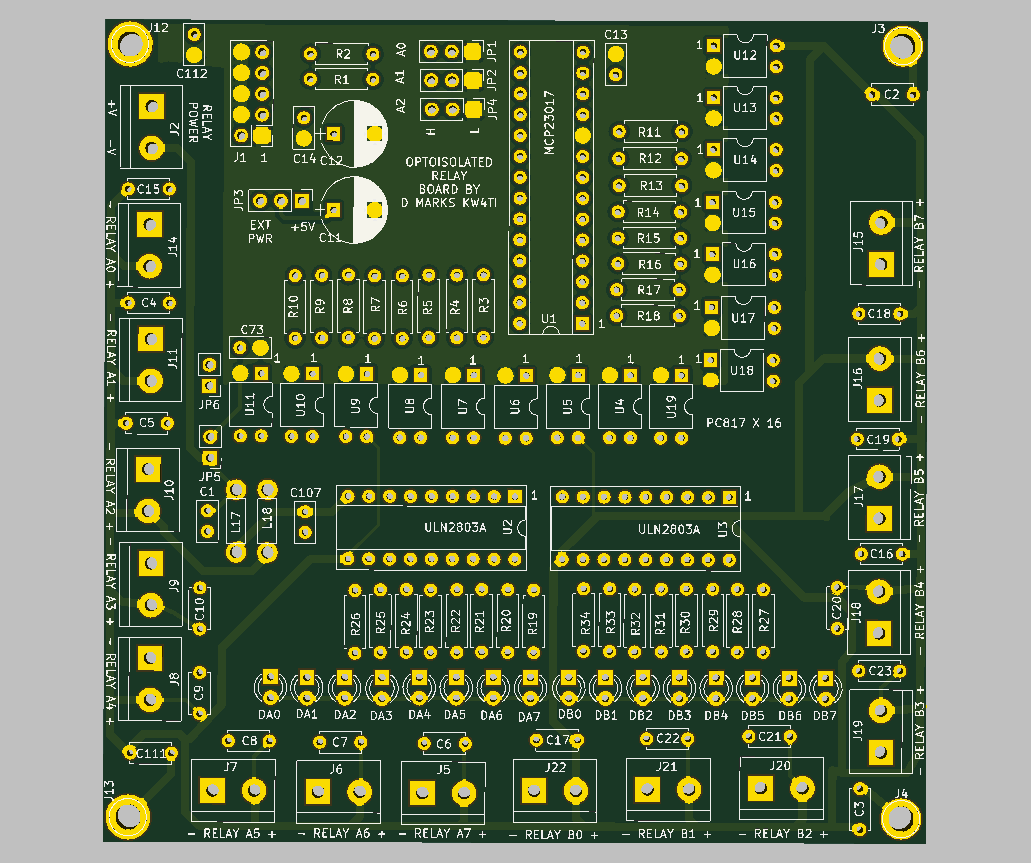
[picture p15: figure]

Simplified Schematic

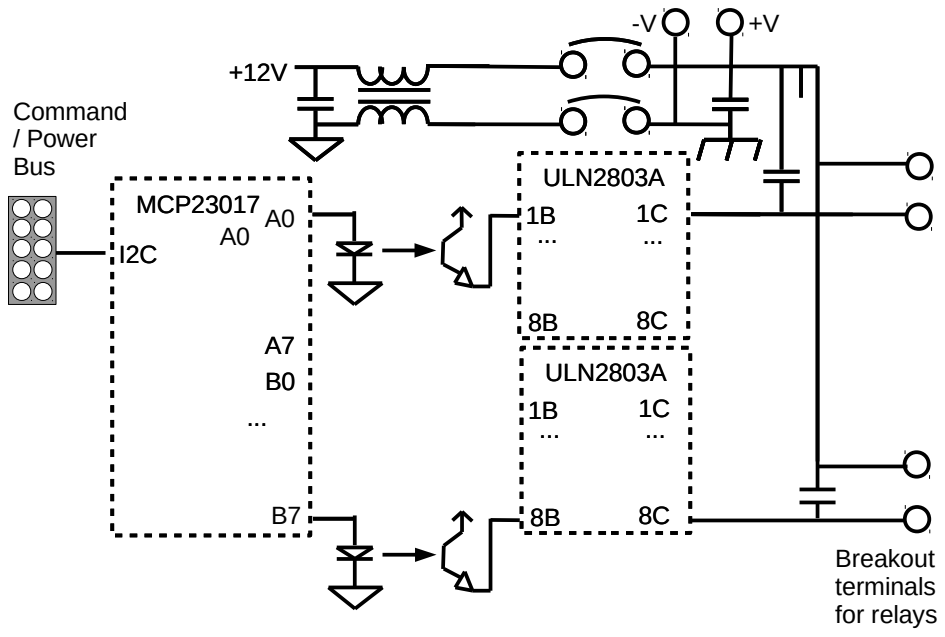
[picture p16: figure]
MCP23017; ULN2803A 1B ...; Command / Power Bus; Breakout terminals for relays

The OptoisolatedRelay module provides a drive for 16 relay coils. The drive circuity is optoisolated from the digital circuitry. The power may be provided by the command/power bus, in which case the jumpers JP5 and JP6 are closed, and the RF is isolated by a common-mode choke. Alternatively, it may be provided by a completely separate supply, in which case the command/power bus is completely galvanically isolated from the relays and RF path. This module is intended to interface to relays that are require isolation because they are in high power RF environments with high voltages, for example, loading parasitic vertical antennas or parasitic elements of a Yagi antenna. Common-modes choke may be placed on the cable sto the relay coils to add further RF isolation. The module should be grounded to the chassis/RF ground through the standoffs at the corners of the PCB as even with optoisolators, any RF signal at the PCB must be shunted.

## BigRelays and LittleRelays Modules

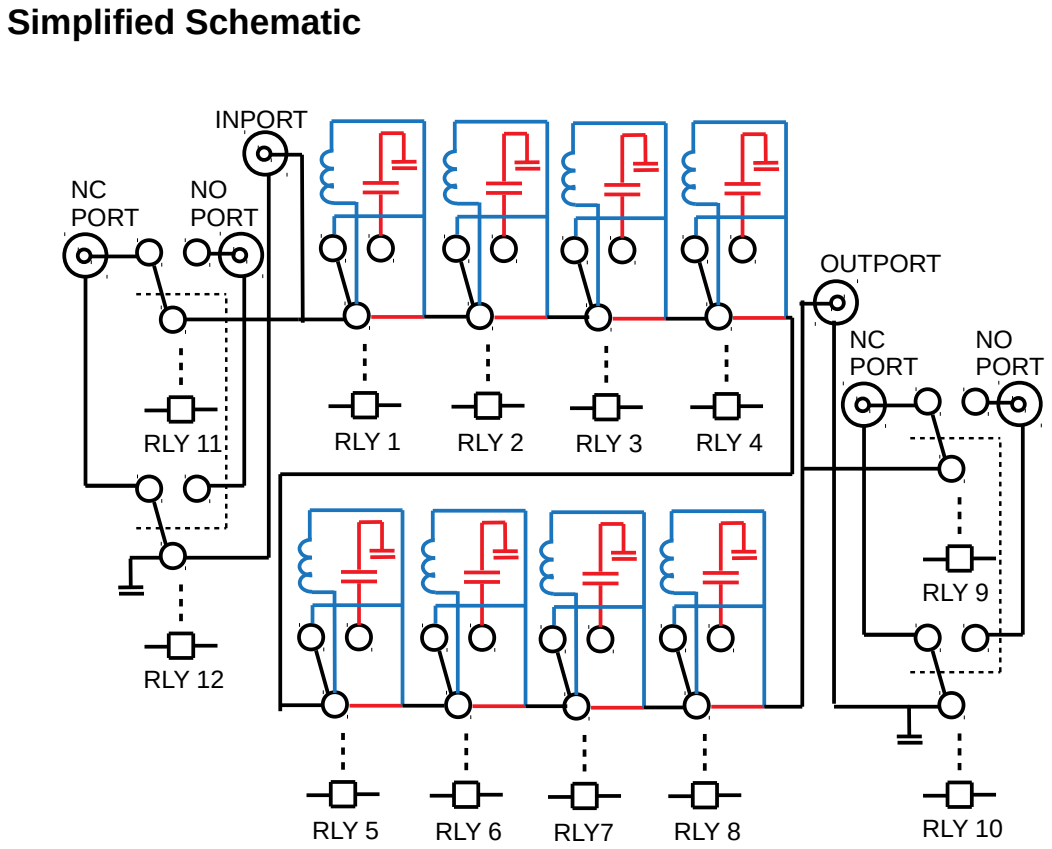
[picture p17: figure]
Simplified Schematic; RLY 12; RLY 11; NC PORT; NO PORT; INPORT; RLY 1; RLY 2; RLY 3; RLY 4; RLY 5; RLY 6; RLY7; RLY 8; RLY 10; RLY 9; OUTPORT

The BigRelays and LittleRelays boards can connect either series inductors or parallel capacitors to the RF path. The blue components in the schematic note the paths taken when wired for series inductors, and the red paths are for the parallel capacitor configuration. It takes a 2-by-10 IDC ribbon cable that connects to J17. These control 10 relays. Eight of these relays, RLY1-RLY8, select an inductor or capacitor for the RF path. RLY9 and RLY10 form a DPDT switch that selects one of two ports, port J10 (normally closed) or J9 (normally open) for the RF and ground connection of that side of the board to be connected to, while J18 is always connected. Likewise, RLY11 and RLY12 form a DPDT switch that selects one of two ports J16 (normally closed) or J11 (normally open), with J8 always connected. Therefore either side of the series inductors or parallel capacitors may be connected to two different ports. This allows, for example, a module to be changed from being a series to shunt element, or allows the module to be connected to different parts of a matching network. There is silkscreening on the back of this board marking the RF and GND pads of the normally closed, normally open, and always connected terminals.

Whether the board uses series or parallel elements is selected using the jumpers J1, J2, J3, J4, J5, J6, J7, and J19. Each of these jumper points looks similar to:

To select the series configuration, solder a jumper wire between the center pad and the pad marked “L” for inductor, or for the parallel configuration, solder a jumper wire between the center pad and the pad marked “C” for capacitor. All of these jumper points should be soldered the same way. Then the component is soldered to pads that appear as:

If the series inductor configuration is used, the component should be soldered between the two circular pads that have an inductor symbol connection them. If the parallel capacitor configuration is used, one or more capacitors may be soldered between the two long pads. Both sets of pads should not be used at the same time.

The relay coils are grounded to the chassis through the capacitors C11, C24, and C25 to the lower left standoff. At least one capacitor should be placed here with a 630 V rating and 10 nF capacitance.

On the BigRelays board, points J21, J22, J23, J24, and J25 are connections to the grounds of the RF path, which except for J23 are switched by the relays. These may be connected by jumper wires to the point J27, J28, J29, and J30 which are connected to the standoffs, so that the RF path may be grounded if needed. For example, generally when using capacitors in a shunt configuration, J23 is connected to ground through a jumper wire. On the LittleRelays board, the points J20, J21, J22, J23, and J24 are connections to the grounds of the RF path, and the points J25, J26, J27, and J28 are connected to the standoffs.

Optionally, resistors and LEDs may be fitted so that the state of the relay coils may be seen by which LEDs are illuminated.

For use at the 160 meter band, a maximum capacitance of about 4000 pF is needed. Therefore the capacitors may be picked to be related to each other by near powers-of-two with 2000 pF as the maximum capacitance. The capacitors are usually ceramic or silver mica capacitors rated 1 kV or higher depending on power levels. Multiple capacitors are generally used in parallel to minimize effective series resistance. Some suggestions for values:

2000 pF = 1000 pF || 1000 pF
1980 pF = 470 pF || 470 pF || 470 pF || 470 pF || 100 pF
987 pF = 470 pf || 470 pF || 47 pF
980 pF = 220 pF || 220 pf || 220 pF || 220 pF | 100 pF
500 pF = 100 pF || 100 pF || 100 pF || 100 pF || 100 pF

487 pF = 220 pF || 220 pF || 47 pF
257 pF = 47 pF || 47 pF || 47 pF || 47 pF || 47 pF || 22 pF 247 pF = 100 pF || 100 pF || 47 pF
127 pF = 47 pF || 47 pF || 33 pF
124 pF = 47 pF || 47 pF || 10 pF || 10 pF || 10 pF
120 pF = 22 pF || 22 pF || 22 pF || 22 pF || 22 pF || 10 pF 62 pF = 22 pF || 22 pF || 18 pF
32 pF = 22 pF || 10 pF
16 pF = 33 pF in series with 33 pF
9 pF = 18 pF in series with 18 pF

For the small capacitance values, an open stub of RG-58 or RG-316 may be used, which have a capacitance of approximately 100 pF/m. If the measured capacitance values are programmed into the Controller, the Controller software exhaustively finds the best approximation of capacitances to a particular desired value. Because stray capacitances for the PCB are on the order of several pF, the precision of the capacitors need not be excessive.

For inductors, a maximum capacitance of about 20 uH is needed for the 160 meter band. One way to achieve this is to use stacked T68-2 iron powder toroids, which can be purchased in quantity cheaply:

10 uH = 4 stacked T68-2 cores, 21 turns
5 uH = 2 stacked T68-2 cores, 21 turns
2.5 uH = one T68-2 core, 21 turns
1.25 uH = one T68-2 core, 15 turns
0.63 uH = air core 5 turns of 1 mm diameter magnet wire around 20 mm diameter form 0.32 uH = air core 4 turns of 1 mm diameter magnet wire around 15 mm diameter form 0.16 uH = air core 3 turns of 1 mm diameter magnet wire around 12 mm diameter form 0.08 uH = air core 2 turns of 1 mm diameter magnet wire around 12 mm diameter form

## DelayLine Module

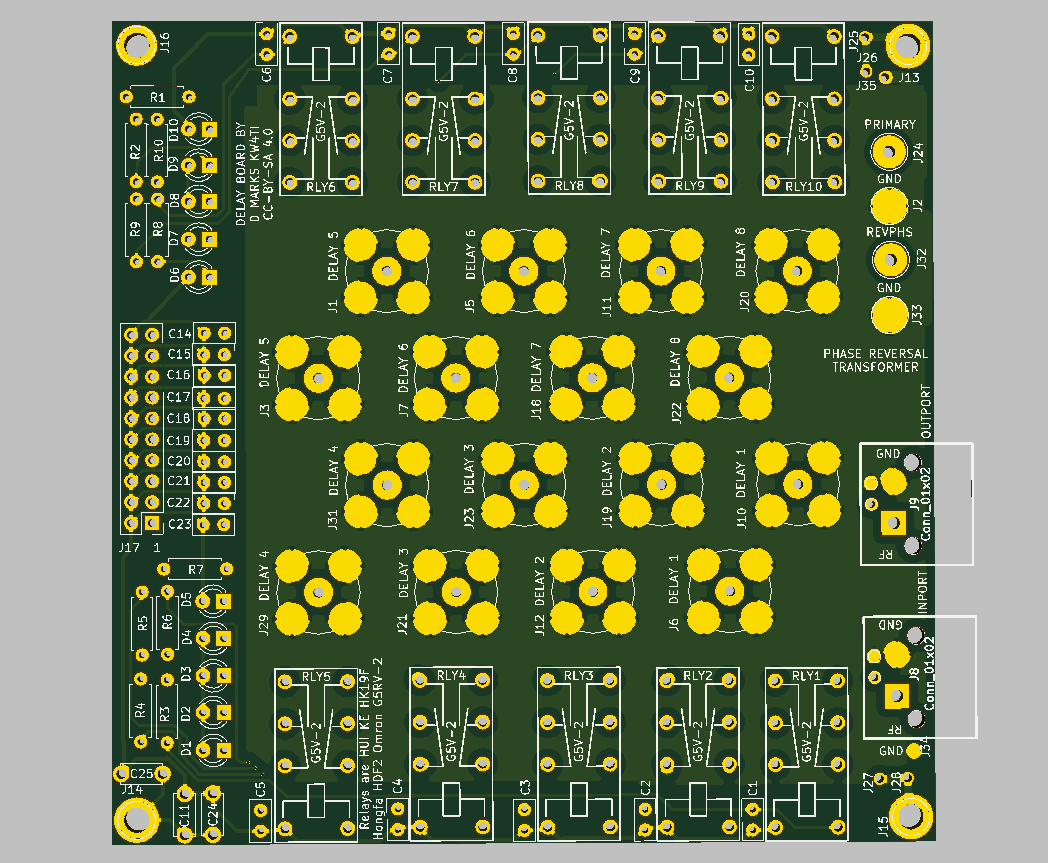
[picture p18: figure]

Simplified Schematic

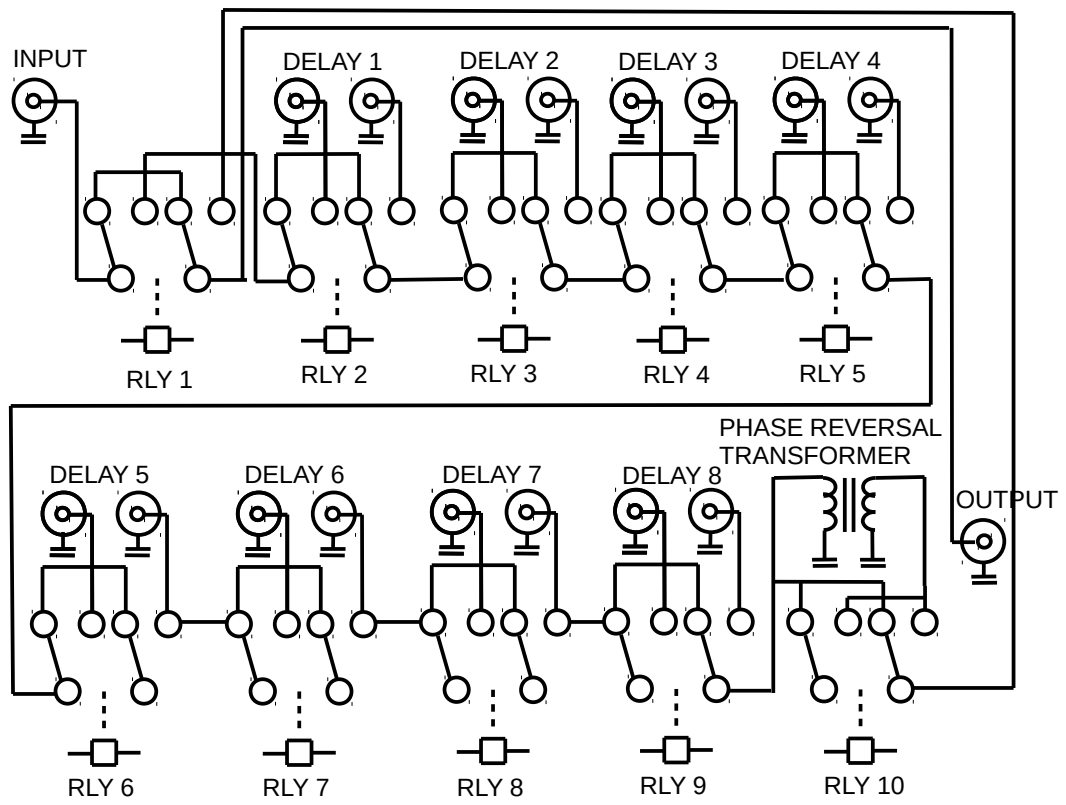
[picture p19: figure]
DELAY 1; RLY 2; INPUT; RLY 1; DELAY 2; RLY 3; DELAY 3; RLY 4; DELAY 5; RLY 6; DELAY 6; RLY 7; DELAY 7; RLY 8; RLY 9; DELAY 4; RLY 5; DELAY 8; RLY 10; OUTPUT; PHASE REVERSAL TRANSFORMER

The DelayLine module generates a selectable delay by adding lengths of coaxial cable into the RF path. Like the BigRelays and LittleRelays modules, the DelayLine module is intended to be connected to a RelayControl module. The DelayLine and LittleDelayLine modules use only the “Little” Relays, not the “Big” Relays, because the Big Relays do not fit on a 10 by 10 cm board, and the Big Relays are SPDT not DPDT.

A length of BNC connectorized coaxial cable is intended to be placed between the two connections marked for the given relay, for example J6 and J10 are for DELAY 1. Up to eight coaxial cables may be switched into the path, switched by RLY2-RLY9. The input port J8 and output port J9 are symmetric and the ports may be exchanged. These ports have the dual footprint that allows either a BNC right-angle connector or a two position screw terminal block to be used. RLY1 is the bypass relay, which in the normally closed position bypasses all of the delays and directly connects the input and output ports.

RLY10 controls phase reversal. A common-mode choke placed at J24, J32, J33, and J2 is used to invert the phase of the signal. The normally closed position selects a signal that is not phase reversed, while the normally open selects the phase reversed signal. Using a phase reversal transformer, enough total delay is needed to apply half a wave of retardance at a frequency, with the phase reversal transformer adding 180º so that an entire wave of retardance may be achieved. Typically the longest delay coaxial cable corresponds to a quarter wavelength or 90º at the lowest frequency used, with each subsequent cable being half the length of the next longer cable. For example, to cover the 10-80 m band, an equivalent 20 m of delay in free space would be required to achieve a 90º phase delay at the 80 m band. For RG-58 with a 0.66 velocity factor, this corresponds to 13.2 m of cable. The next seven cables could be selected so that each has half the delay, for example 6.6 m, 3.3 m, 1.65 m, 83 cm, 41 cm, 20.5 cm, and 10.2 cm. At the shortest wavelength 10m, the ability to adjust the delay with 10.2 cm steps corresponds to a phase resolution of 5.5º. This phase resolution is likely much smaller than required unless the absolute maximum gain must be obtained from an antenna array. The total length of cable required is always less than half a wavelength at the lowest frequency, or 26.4 m for RG-58 at 80 m wavelength.

To ground the BNC shield to the RF chassis ground at the board, the pad J34 may be connected via a jumper wire to any of J25, J26, J27, or J28.

## ReversibleBigSection and ReversibleLittleSection Modules

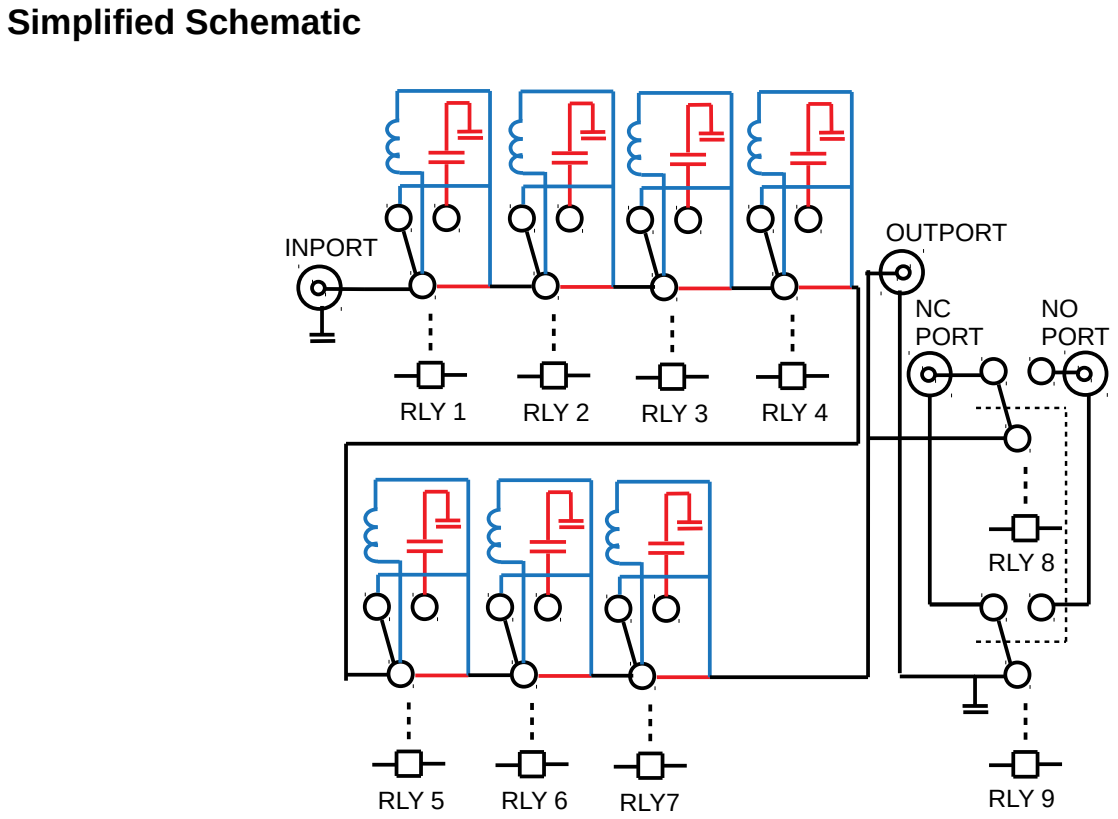
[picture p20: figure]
Simplified Schematic; INPORT; RLY 1; RLY 2; RLY 3; RLY 4; RLY 5; RLY 6; RLY7; RLY 9; RLY 8; NC PORT; NO PORT; OUTPORT

The ReversibleBigRelays and ReversibleLittleRelays modules combine the I2C decoding circuity, relays, and series inductors or parallel capacitors on the same PCB. The blue components on the schematic indicate the paths taken when configured as series inductors, and the red paths when configured as parallel capacitors. Because of this, there is less isolation between the RF path and the digital circuitry than when a separate RelayControl module is used. These modules control up to seven relays RLY1-RLY7, each of which switch a series inductor or parallel capacitor. The two relays RLY8 and RLY9 switch the output port RF and GND between a normally closed port J9 and normally open port J10. The port J23 is always connected. This switchable port may be used to reconfigure the network. For example, it may be used to implement a bypass function by shorting out the matching network, or alternatively it may be used to switch a L network from a low Z to high Z configuration.

The RF connections to the board are combined footprints that accommodate either a BNC right-angle connector or a 2 position screw terminal block.

To configure the module to be either series inductors or parallel capacitors, the pads J1, J2, J3, J4, J5, J6, and J7 must be jumpered. These look like:

To configure as a series inductor, a jumper is soldered between the center pad and the L pad. To configure for parallel capacitors, a jumper is soldered between the center pad and the C pad. All of the pads should be soldered the same way. The inductors or capacitors are soldered to the following pads:

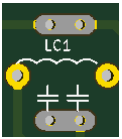
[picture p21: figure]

If the series inductor configuration is used, the component should be soldered between the two circular pads that have an inductor symbol connection them. If the parallel capacitor configuration is used, one or more capacitors may be soldered between the two long pads. Both sets of pads should not be used at the same time.

The RF grounds are at pads J16, J17, and J22, with J17 being normally open switched ground and J22 being normally closed switched ground. These may be connected to chassis grounded standoffs through the pads J18, J19, J20, and J21 with jumper wires. The relay coils are grounded to the chassis through capacitors C14 and C35.

For use at the 160 meter band, a maximum capacitance of about 4000 pF is needed. Therefore the capacitors may be picked to be related to each other by near powers-of-two with 2000 pF as the maximum capacitance. However, because there are only seven switchable capacitors, the capability of the tuner to match the load with a low reflection at the 10 m band may diminished as the minimum adjustable capacitance increment is 15 pF. If a lower SWR is required on the higher bands, a smaller maximum capacitance may be desirable. The capacitors are usually ceramic capacitors or silver mica rated 1 kV or higher depending on power levels. Multiple capacitors are generally used in parallel to minimize effective series resistance. Some suggestions for values:

2000 pF = 1000 pF || 1000 pF
1980 pF = 470 pF || 470 pF || 470 pF || 470 pF || 100 pF
987 pF = 470 pf || 470 pF || 47 pF
980 pF = 220 pF || 220 pf || 220 pF || 220 pF | 100 pF
500 pF = 100 pF || 100 pF || 100 pF || 100 pF || 100 pF 487 pF = 220 pF || 220 pF || 47 pF
257 pF = 47 pF || 47 pF || 47 pF || 47 pF || 47 pF || 22 pF 247 pF = 100 pF || 100 pF || 47 pF
127 pF = 47 pF || 47 pF || 33 pF
124 pF = 47 pF || 47 pF || 10 pF || 10 pF || 10 pF

120 pF = 22 pF || 22 pF || 22 pF || 22 pF || 22 pF || 10 pF 62 pF = 22 pF || 22 pF || 18 pF
32 pF = 22 pF || 10 pF
16 pF = 33 pF in series with 33 pF
9 pF = 18 pF in series with 18 pF

For the small capacitance values, an open stub of RG-58 or RG-316 may be used, which have a capacitance of approximately 100 pF/m. If the measured capacitance values are programmed into the Controller, the Controller software exhaustively finds the best approximation of capacitances to a particular desired value. Because stray capacitances for the PCB are on the order of several pF, the precision of the capacitors need not be excessive.

For inductors, a maximum capacitance of about 20 uH is needed for the 160 meter band. One way to achieve this is to use stacked T68-2 iron powder toroids, which can be purchased in quantity cheaply:

10 uH = 4 stacked T68-2 cores, 21 turns
5 uH = 2 stacked T68-2 cores, 21 turns
2.5 uH = one T68-2 core, 21 turns
1.25 uH = one T68-2 core, 15 turns
0.63 uH = air core 5 turns of 1 mm diameter magnet wire around 20 mm diameter form 0.32 uH = air core 4 turns of 1 mm diameter magnet wire around 15 mm diameter form 0.16 uH = air core 3 turns of 1 mm diameter magnet wire around 12 mm diameter form 0.08 uH = air core 2 turns of 1 mm diameter magnet wire around 12 mm diameter form

## LittleDelayLine Module

Simplified Schematic

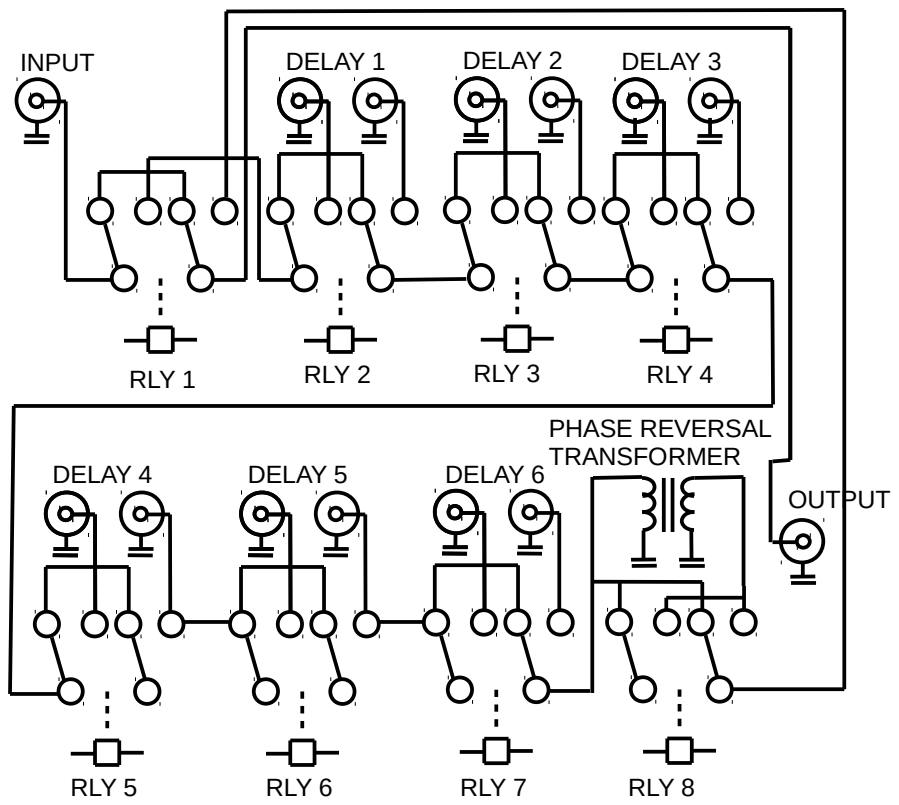
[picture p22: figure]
DELAY 1; RLY 2; INPUT; RLY 1; DELAY 2; RLY 3; DELAY 3; RLY 4; DELAY 4; RLY 5; DELAY 5; RLY 6; DELAY 6; RLY 7; RLY 8; OUTPUT; PHASE REVERSAL TRANSFORMER

The LittleDelayLine module generates a selectable delay by adding lengths of coaxial cable into the RF path. This module combines the I2C control, relays, and coaxial cables on the same PCBs. A length of BNC connectorized coaxial cable is intended to be placed between the two connections marked for the given relay, for example J1 and J2 are for DELAY 1. Up to six coaxial cables may be switched into the path, switched by RLY2-RLY7. The input port J8 and output port J9 are symmetric and the ports may be exchanged. These ports have the dual footprint that allows either a BNC right-angle connector or a two position screw terminal block to be used. RLY1 is the bypass relay, which in the normally closed position bypasses all of the delays and directly connects the input and output ports.

RLY8 controls phase reversal. A common-mode choke placed at J25, J26, J27, and J28 is used to invert the phase of the signal. The normally closed position selects a signal that is not phase reversed, while the normally open selects the phase reversed signal. Using a phase reversal transformer, enough total delay is needed to apply half a wave of retardance at a frequency, with the phase reversal transformer adding 180º so that an entire wave of retardance may be achieved. Typically the longest delay coaxial cable corresponds to a quarter wavelength or 90º at the lowest frequency used, with each subsequent cable being half the length of the next longer cable. For example, to cover the 10-80 m band, an equivalent 20 m of delay in free space would be required to achieve a 90º phase delay at the 80 m band. For RG-58 with a 0.66 velocity factor, this corresponds to 13.2 m of cable. The next five cables could be selected so that each has half the delay, for example 6.6 m, 3.3 m, 1.65 m, 83 cm, and 41 cm. At the shortest wavelength 10m, the ability to adjust the delay with 41 cm steps corresponds to a phase resolution of 22º. This phase resolution is likely adequate to achieve gain with a small antenna array. The total length of cable required is always less than half a wavelength at the lowest frequency, or 26.4 m for RG-58 at 80 m wavelength.

To connect the coaxial cable RF shield to chassis ground at the board, J16 may be jumpered to any of J18, J19, J20, or J21.

## SwitchBus Module

Simplified Schematic

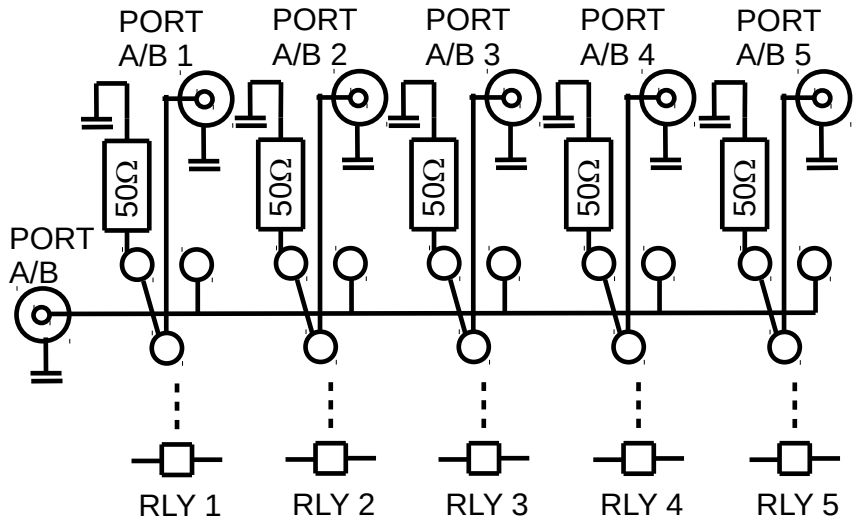
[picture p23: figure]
PORT A/B; RLY 1; PORT A/B 1; RLY 2; PORT A/B 2; RLY 3; PORT A/B 3; RLY 4; PORT A/B 4; RLY 5; PORT A/B 5

The SwitchBus module may be used for many purposes. The port connects a single port A/B to one or more of five ports PORT A/B 1-5. There are two independent switch multiplexers on the module. It may be used, for example, to select an antenna, so that the ModularTuner system may be used as an antenna selector as well. The two multiplexers on the module may be used together, for example, to place a filter into the signal path, or to form a single 5-by-5 multiplexer by joining ports A and B together. The other ports may be terminated or grounded by placing the appropriate resistor on the normally closed contact of the selection relays. This module must be used with a RelayControl as it does not have any I2C drive circuity. When used to select antennas, it is intended to provide the greatest isolation between the antennas that are not selected and the Controller so that any nearby lightning or electrostatic discharges are shunted to ground through the relay normally closed contacts. If used for this purpose, a separate ground connection should be made to this module to provide the path for the discharge.

## LittleSwitchBus Module

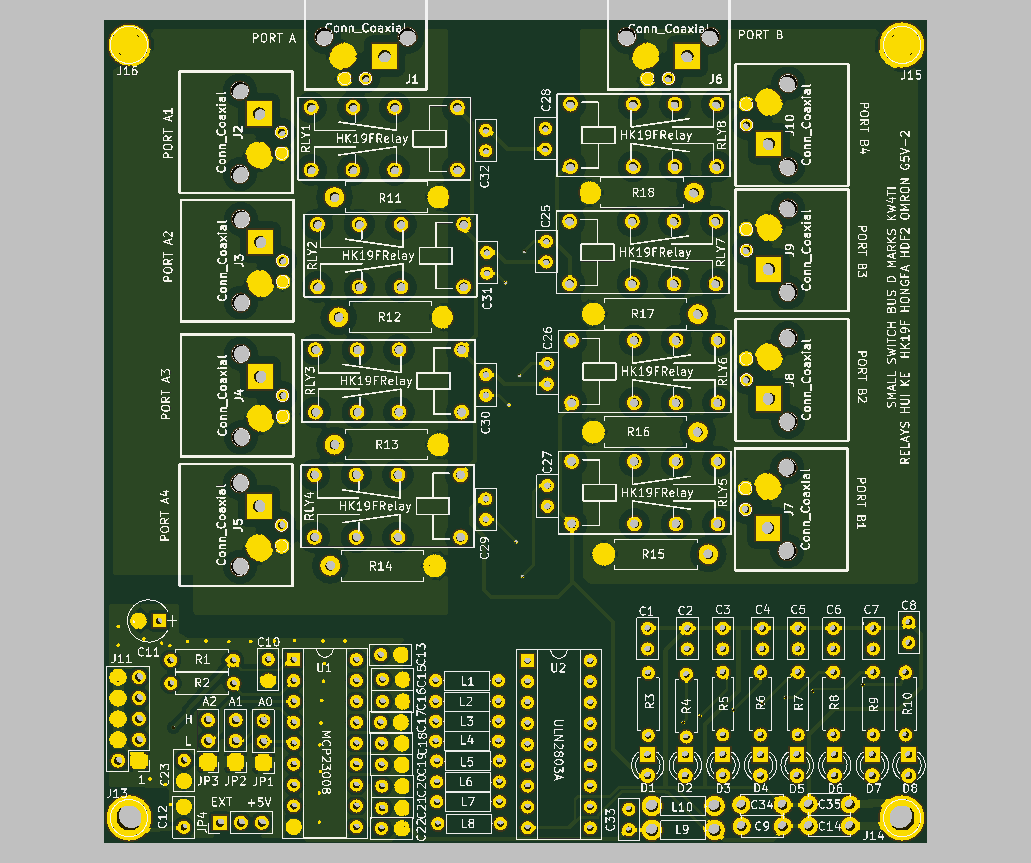
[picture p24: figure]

Simplified Schematic

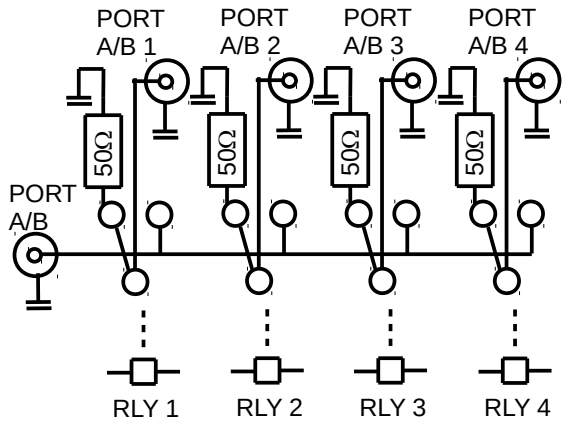
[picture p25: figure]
PORT A/B; RLY 1; PORT A/B 1; RLY 2; PORT A/B 2; RLY 3; PORT A/B 3; RLY 4; PORT A/B 4

The LittleSwitchBus is similar to the SwitchBus except that it contains the I2C decode circuity and selects one of four rather than one of five relays, and the relays are the “small” relays. Because of this, it has less isolation than the SwitchBus module. The port connects a single port A/B to one or more of five ports PORT A/B 1-4. There are two independent switch multiplexers on the module. It may be used, for example, to select an antenna, so that the ModularTuner system may be used as an antenna selector as well. The two multiplexers on the module may be used together, for example, to place a filter into the signal path, or to form a single 5-by-5 multiplexer by joining ports A and B together. The other ports may be terminated or grounded by placing the appropriate resistor on the normally closed contact of the selection relays. The LittleSwitchBus is useful for selecting taps on a transformer, for example, to change the ratio of an impedance transformation.

## QuadCoupler Module

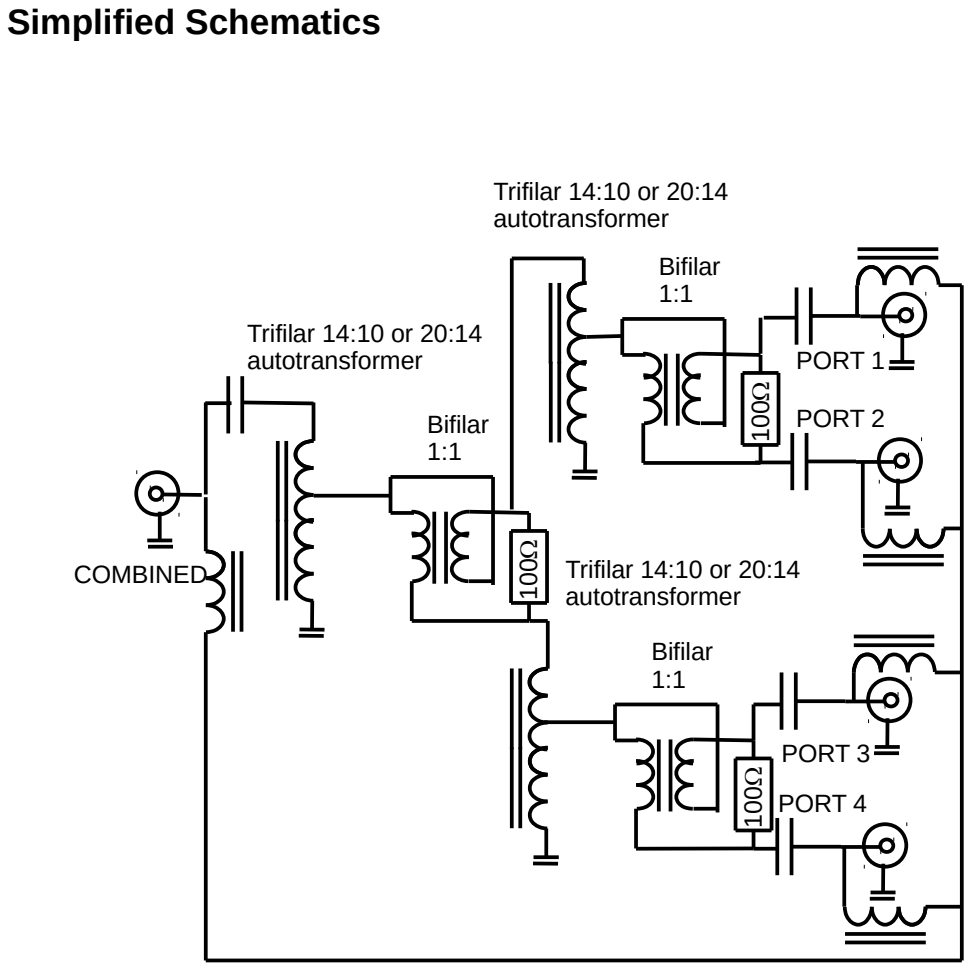
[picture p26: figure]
Simplified Schematics; Trifilar 14:10 or 20:14 autotransformer; COMBINED; Bifilar 1:1; PORT 1; PORT 2; PORT 3; PORT 4

The QuadCoupler contains three Wilkinson dividers that split the incident power nearly equally among four antenna ports. The power is incident at J3 and is divided to J2, J4, J5, and J6. The Wilkinson dividers consist of two transformers, one of which transforms the load impedance from 50 to 25 ohms, and another which divides the 25 ohm impedance over two 50 ohm ports. DC power may be injected using bias-tees into each of the output ports at J11, J13, J15, and J17. DC power may be coupled from the input port J16. There are peak detectors built into the board to measure the voltage at each of the output ports to ensure that the power split is equal. The combined footprints are used so that BNC right-angle PCB connectors or two position screw terminal blocks may be soldered to the board.

## LCDadapter Module

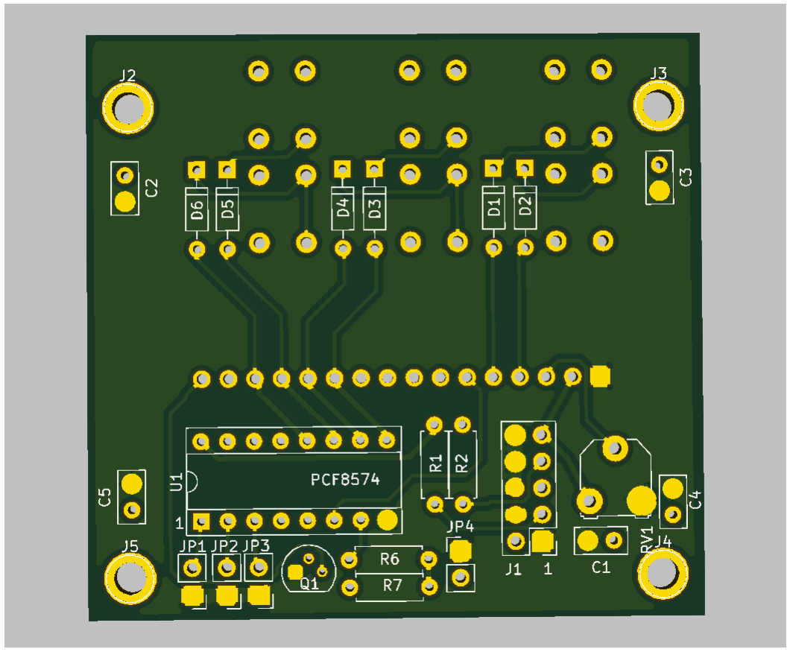
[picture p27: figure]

The LCDadapter module is an I2C adapter that is soldered to a HD44780 display. It is modified from the conventional PCF8574 I2C to HD44780 adapters commonly available by adding six push buttons that may be read through I2C that may be used to control the ModularTuner. A conventional PCF8574 adapter may be easily modified to add the six buttons and therefore this module can be made from the commercially available PCF8574 I2C displays. This module is being made available for those who would rather have a predesigned module compatible with the Controller rather than modify a commercial module, and this PCB has the same grounding conventions used by the other modules to best ensure RFI immunity.

If used with the push buttons, the transistor Q1 should be omitted and JP4 should be closed. To make the backlight respond to commands as in the commercial modules, Q1 should be present and JP4 opened.

# A simple L-match tuner for 100 watts maximum power

The wiring diagram of a simple L match tuner using four modules is shown below:

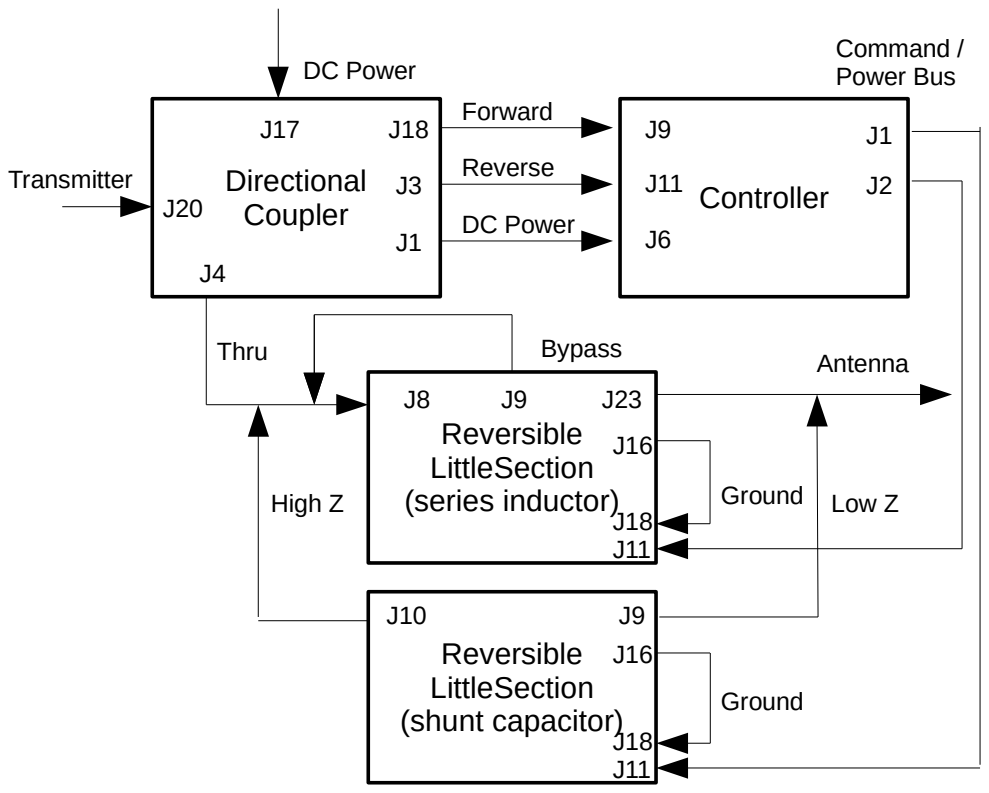
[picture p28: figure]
Controller Directional Coupler; Forward; J11 Reverse; DC Power; Transmitter; Reversible LittleSection (series inductor); Thru; Antenna; Bypass; Reversible LittleSection (shunt capacitor); Ground; High Z; Command / Power Bus; Low Z

The power from the transmitter is incident on the Directional Coupler at the input port J20. The forward power is sampled to port J18 and is connected to port J9 on the controller. Likewise, the reverse power is sampled at port J3 and connected to port J11 on the controller. The DC power is connected from J1 on the DirectionalCoupler to J6 on the Controller.

There are two ReversibleLittleSection modules, one wired as series inductors and another as shunt capacitors. The thru connection of the DirectionalCoupler on J4 is connected to the inductor section at its input port J8. The switchable port relay is connected so that its normally closed port J9 is connected to J8 so that when the tuner is in bypass mode, the inductors are shorted out. The always connected port J23, is connected to the antenna. The other ReversibleLittleSection with shunt capacitors module is connected to either the input or output port of the inductor module, with the normally closed J9 port connected for a low impedance L-matching network, and the normally open port J10 connected for a high impedance L-matching network. On both sections, J16 is connected to J18 to connect the RF ground to the chassis, and there are Command/Power bus connectors connected from the Controller to both modules.

# L-match tuner for greater than 100 watts power

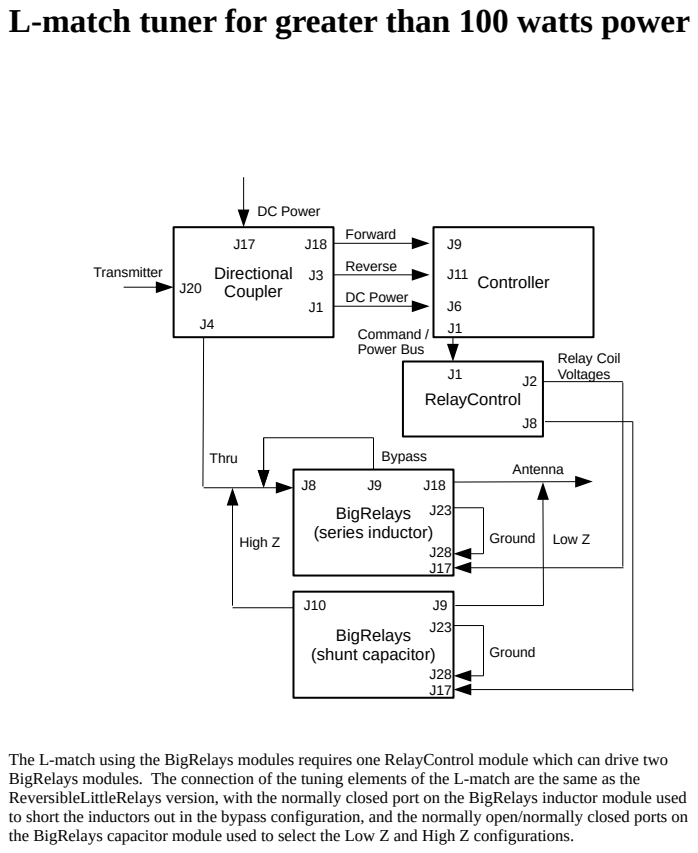
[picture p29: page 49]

The L-match using the BigRelays modules requires one RelayControl module which can drive two
BigRelays modules. The connection of the tuning elements of the L-match are the same as the
ReversibleLittleRelays version, with the normally closed port on the BigRelays inductor module used
to short the inductors out in the bypass configuration, and the normally open/normally closed ports on
the BigRelays capacitor module used to select the Low Z and High Z configurations.

# Balanced vs. unbalanced tuners

The L-match configurations shown are for unbalanced transmission lines such as coaxial cable and vertical antennas with the outer conductor of the cable at a fixed potential. Balanced transmission lines such as ladder line or open wire feedline require opposite potentials on the two conductors. There are two approaches to modifying a tuner to feed a balanced transmission line.

One approach is to design a network that is symmetric. For example, a L-network may be modified by inserting two identical inductances in series with both conductors of the transmission line. While in principle this works, in practice it is difficult to achieve good balance. Not only must be inductances be matched, other asymmetric effects such as stray capacitances must also be identical for the two conductors. Furthermore, this method adds cost and complication over alternative methods.

A second approach is to put a common-mode choke balun on the output of an unbalanced L-network. The common-mode choke balun forces the currents in the two conductors to be equal. For high power, a high voltage is developed across the because of the high impedance of the balun multiplies any common mode current. The choke should be placed on a short coaxial cable less than a meter from the tuner in a well-insulated plastic box. The choke can be constructed from 10-15 turns of coaxial cable on one or two FT240-31 or FT240-43 stacked toroidal ferrite cores depending on the power levels used. Terminals for the open wire feedline can be joined to the coaxial cable after passing through the balun. This approach is simple, and the cost of two FT240-43 is often less than constructing another relay module. The only disadvantage of this approach is that there are high voltages developed across the balun so that the balun should be kept away from sensitive equipment.

# Phase measurement, phasing the array, and the antenna current sense transformer

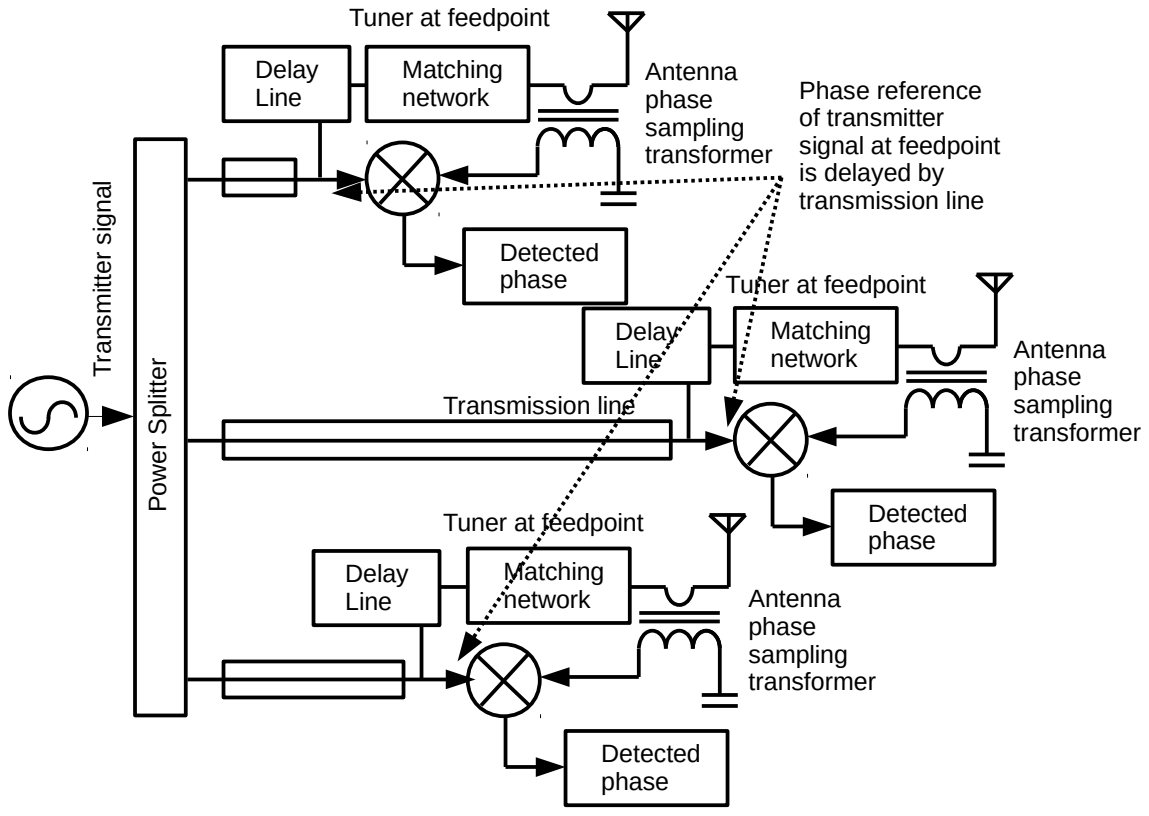
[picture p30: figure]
er Splitter; Transmitter signal; Transmission line; Matching network; Antenna phase sampling transformer; Detected phase; Tuner at feedpoint; Phase reference of transmitter signal at feedpoint is delayed by transmission line; Delay Line

One of the unique aspects of this antenna tuner design is the ability to sense the phase of the antenna current. This enables feedback so that the phase of the antenna current may be adjusted by a switched delay line to achieve a desired radiated phase. The relative phase between the forward signal and the current is measured as the forward signal phase is independent of any reflections or imperfect matching of the antenna. The forward signal at the tuner serves as a phase reference for both the antenna current and the reflected signal phases. Because the forward signal originates at the transmitter, the delay of the signal originating at the transmitter propagating to each tuner must be characterized if the phase relationship between the signals at the antenna tuners is to be known. For example, equal cable lengths between the transceiver and the tuners may be used so that the delays to each antenna tuner are equal and therefore the phases are the same at all frequencies. However, this is not necessary if a switched delay line is used such as the DelayLine module, as the phase can be adjusted at the feedpoint to compensate both for unequal delays to the tuners as well as orient the radiation in a desired direction.

The phased array arrangement that is implemented by the ModularTuner is somewhat unusual. Typically, the power must be divided between the antennas and the correct phasing applied to compensate for any mutual impedance or coupling between the antennas as to achieve the greatest gain. Because of this, most phased arrays work only for a limited number of bands and produce a limited number of radiation patterns. It is desired to use the ModularTuner to experiment with arrangements of phased arrays that take advantage of impedance matching at the feedpoints of each antenna as well as the dynamic phase adjustment of each antenna. Because the ModularTuner at present has no modules to adjust the power balance between the antennas, the gain must be optimized with equal power radiated from all antennas. This in general does not produce as high of gain as if the power could be arbitrarily allocated between antennas.

Due to the mutual impedance between the antennas, the radiation resistance of an antenna can be significantly reduced or even be negative in extreme cases. One of the advantages of having adjustable tuning elements at the feedpoint is that within a certain range of impedances, the impedance matching network can compensate for the variations in the radiation resistance of an antenna caused by its interactions with other antennas. To minimize this problem, the antennas in the array may be placed such that they are separated by distances at least the length of the antenna elements themselves.

If the antennas can be impedance matched such that they radiate equal amounts of power, the delay can be adjusted independently of the impedance transformation as the delay is applied between the transmitter and the antenna matching network by adding variable amounts of coaxial cable to the signal path. Then the antenna current sense transformer can be used to determine the phase of the radiated current given the applied delay.

If the delays to all of the antennas have been calibrated, then by using the known phase of the forward signal at the antenna feedpoint, the phase can be set such that all of the antennas have a known relative phase relationship. However, in practice, one is often trying to direct a beam towards a particular station. In this case, this station can serve as the reference signal to adjust the antenna phases and accurate phase calibration of the array is not required. By adjusting the delays at each antenna to maximize the signal strength from the station, the array forms a beam directed towards that station. If the direction to the station is known, the phases used to direct the beam to the station may be recorded and reused when one wishes to direct the beam back in the same direction at the same frequency. When trying to reach a distant station, it may be more useful to optimize the phase to receive the greatest signal so that the transmitted signal likewise has additional gain. While such an arrangement may not achieve the best gain over an antenna array designed to radiate in particular fixed directions for a particular band, it may be much more useful in practice to achieve a moderate amount of gain in any direction on many different bands.

Another advantage of this method is that an exact arrangement of the antennas is not required, and so antennas in the phased array may be placed in a staggered or irregular pattern as long as they are sufficiently separated. Furthermore, having impedance matching for each antenna in the array enables a heterogeneous set of radiators to be used, so that wires may be placed of varying lengths or perhaps even metallic objects in the environment can be used as radiators. The agility of such a system may be more useful in practice.

Another possibility to be explored in the future is to derive a known phase signal from a GPS disciplined oscillator (GPSDO) at each feedpoint. The phase of the forward wave may be measured relative to the common phase of the GPSDO at each feedpoint and this phase may be used to calibrate the delay to the feedpoint. There is a port for a NEO7M GPS module on the Controller that can be used to find the position of the antenna feedpoint as well as derive a frequency that is a multiple of 1 Hz with an edge synchronized to the beginning of each second.

The antenna current sense transformer is typically constructed from 15 secondary turns around a FT50-43 ferrite toroid. The wire or coaxial cable carrying the antenna current should be inserted through the toroid and is the one primary turn. It is important to insert the wire through the center of the toroid so that it does not pass near the secondary and capacitively couple to it. If a coaxial cable is used, it should be grounded at only one end to act as a Faraday shield. The secondary should be connected to the Controller board and is terminated by a 50 ohm resistor. The wires connected to the Controller should be twisted together to minimize the loop area. If there is still excessive capacitive coupling between the primary and secondary of the antenna current sense transformer, a the connection to the Controller can be wrapped several times around a ferrite toroid as a common-mode choke. This may be necessary for high power as even a small amount of capacitive coupling may result in excess common-mode signal.

# Appendices

## Commands for the antenna tuner

The commands that may be issued over the USB serial interface or the Wireless interface when in remote control mode are documented here.

HELP

Display the list of commands and their arguments.

READSTATE <state number>

Read the configuration from the memory <state number>. There are currently four locations numbered 1 to 4 to store configurations.

WRITESTATE <state number>

Write the current to from the memory <state number>. There are currently four locations numbered 1 to 4 to store configurations.

SAVECACHE <frequency khz>

Write the current state of the relays 1 to 3 to the tuning state cache with an entry at the frequency given by <frequency khz>.

RECALLCACHE <frequency khz>

Read the state of the relays 1 to 3 from the tuning state cache with an entry at the frequency given by <frequency khz> and change the relays to this state.

SHOWCACHE

Show the tuning parameters of all entries in the tuning state cache in the order of most recently used entry to least recently used entry.

CLEARCACHE

Erase all entries in the tuning state cache. Any subsequent tuning cycles require an exhaustive tune to find a match at the target reflection magnitude and will be stored in the cache once found.

TUNER?

Show the state of the tuning configuration. A list of entries and their corresponding values are displayed in the form <entry name>=<entry value>.

SETTUNER <entry name>=<entry value>

Change an entry in the tuning configuration. For example, to change the maximum reflection permitted for a tune to 0.3, use the the command “SETTUNER MAXREFLECTION=0.3”. These changes are not saved immediately. They can be committed to flash using the WRITESTATE command or will be automatically saved after five minutes. The same format is used for <entry name>=<entry value> as is displayed by the TUNER? command.

TESTRELAY <relay #> <is switch?> <relay/switch number> <setting>

Manually turn on/off a relay on a RelayModule to test its function. The relay module number is given by <relay #>, a number from 1 to 8. <is switch?> is equal to 1 for testing one of the port selection switch relays, and 0 for testing one of the component selector relays. <relay/switch number> is the number of the component selector or port selection switch relay. Currently the switch number is either 1 or 2, and the number of component selector relays can be up to 16. Finally <setting> is zero or one, 0 being an open relay and 1 being a closed relay. For example, to set component relay 3 on relay number 2 to the closed state, use “TESTRELAY 2 0 3 1”.

SETRLY <relay #> <relay value> <method>

Set the relay module <relay #> to be tuned to the value <relay value>. method=0 for choosing the closest available value to the desired value, method=1 chooses the closest available value strictly less than the desired value, and method=2 chooses the closest available value strictly greater than the desired value. For example, if relay module 1 is an inductor relay module, and one wishes to set its value to 1234 nH or the closest available value, use “SETRLY 1 1234 0”.

RLYDEF <relay #> <default number #>

Set the entry for a relay module numbered <relay #> to a default configuration. This is how a new relay entry is activated. The following default configurations are available:

0 = blank an entry and disable the relay module
1 = BigRelays/LittleRelays module set up for series inductors
2 = BigRelays/LittleRelays module set up for parallel capacitors
3 = DelayLine module
4 = ReversibleBigSection/ReversibleLittleSection module set up for series inductors
5 = ReversibleBigSection/ReversibleLittleSection module set up for parallel capacitors
6 = LittleDelayLine module

It is likely necessary that the values of the components need to be changed from the default values.

RELAY?

Print out the configuration information of all the relays in the form <entry name>=<entry value>.

SETRELAY <relay #> <entry name>=<entry value>

Set the entry labeled <entry name> on relay module <relay #> to the given <entry value>. The format of <entry name>=<entry value> the is the same as shown in the RELAY? command.

TUNE <tuning state>

Set the tuning state to <tuning state>. <tuning state>=0 corresponds to standby mode, which will retune only if excessive reflections are detected. <tuning state>=1 corresponds to “force tune” mode, which will always tune the next time the amount of power is not too low or too high for acceptable tuning. If rig control is enabled, the force tune attempts to send a signal to the rig to send power to tune immediately. <tuning state>=2 is disable tuning if excessive reflections are detected, but does not change the current state of the relays.

STATUS

Display status of tuner, including tuning state, frequency of last tune, SWR, and estimated load impedance.

DEBUG <debug mode>

Turns on debug messages. <debug mode>=0 is debug messages disabled, <debug mode>=1 is debug messages enabled.

BYPASS

Place the tuner into bypass mode. If the tuning state is not set to disable tuning, when excessive reflections are detected, the tuner will initiate a tuning cycle.

REMOTE <remote state>

Turn the remote control over wireless on or off. <remote state>=1 is enable the remote control over wireless, and the command interface is available over wireless. <remote state>=0 is disable the remote control over wireless, and the remote reverts back to the packet interface.

## Tuner configuration entries

The entries that configure the Controller tuner configuration are documented here. They are changed by means of the “SETTUNER” command, and may be saved in flash using the “WRITESTATE” command.

LABEL=<label>

A text label up to 15 characters describing the configuration.

POWERCALIB=<power calib>

A number used to calibrate power in watts from the analog-to-digital measurements of the forward and reverse power.

MINTUNINGPOWER=<min power>

The minimum amount of power needed to initiate a tuning cycle in watts.

MAXTUNINGPOWER=<max power>

The maximum amount of power allowed during a tuning cycle in watts. This is to prevent hot switching with excessive power.

MAXREFLECTION=<reflection coefficient>

The maximum reflection coefficient, between 0.0 and 1.0, allowed before the tuning cycle is successfully completed.

RETUNETHRESHOLD=<reflection coefficient>

The threshold over which the reflection from the antenna must exceed before automatic tuning is initiated. This number is between 0.0 and 1.0.

SEARCHRELAXATION=<relaxation constant>

A number for the search algorithm that determines how greedy the algorithm is. <relaxation constant>=1.0 is the most greedy. The default is 1.05. The number may be increased if tunes can not be found at the expense of more lengthy tuning cycles.

REMOTECHANNELNO=<channel no>

The channel number to assign to the remote wireless radio on startup.

SEARCHKHZSPACING=<khz #>

The maximum difference in frequency between a desired frequency and the frequency of a tuning cache entry to match the entry. The default is 10 kHz.

RIGCONTROL=<rig control>

Turn on rig control. Currently the value rig control numbers are <rig control>=0 for no rig control, or <rig control>=1 for ICOM. This only takes effect after resetting the tuner.

SWITCHBYPASS=<relay #>,<switch #>,<state>,<relay #>,<switch #>,<state>, ...

Specify the state of the switches on the relay modules that place the tuner into the bypass state. The format of these are triads of numbers indicating the relay module number, switch number on the relay module, and the state of either 0 for open or 1 for closed. For example, if switch #2 on relay #1 should be open, and switch #1 on relay #3 should be closed, this would be
“SWITCHBYPASS=1,2,0,3,1,1”. All unused entries should be zero.

SWITCHSTATE1-6=<relay #>,<switch #>,<state>,<relay #>,<switch #>,<state>, …

During a tuning cycle, the switches are set to the states given by SWITCHSTATE1, SWITCHSTATE2, SWITCHSTATE3, SWITCHSTATE4, SWITCHSTATE5, SWITCHSTATE6 in that order. These states encode, for example, high and low Z configurations of a L match tuner, but would configure the switches for other network topologies for more complicated tuning networks. The format of these are triads of numbers indicating the relay module number, switch number on the relay module, and the state of either 0 for open or 1 for closed. See the example in SWITCHBYPASS.

## Relay configuration entries

The entries that configure the Controller relay modules such as the BigRelays/LittleRelays/DelayLine/ReversibleBigSection/ReversibleLittleSection/LittleDelayLine modules are documented here. They are changed by means of the “SETRELAY” command, and may be saved in flash using the “WRITESTATE” command.

MODULETYPE=<moduletype>

Configures the module type. <moduletype>=0 is module disabled, <moduletype>=1 is series inductor module, <moduletype>=2 is parallel capacitor module, and <moduletype>=3 is delay module.

NORELAYPORTS=<number of relays>

Number of digital outputs on the board dedicated to selecting components. Some digital outputs control two relays.

NOSWITCHES=<number of switches>

Number of digital outputs on the board dedicated to switching between ports. Some digital outputs control two relays.

MCP23017=<state>

Chooses whether the module contains a MCP23008 or MCP23017. <state>=0 for a MCP23008 and <state>=1 for a MCP23017.

I2CADDR=<hex address>

Configures the I2C address of the relay module. This number is specified in hexadecimal.

AUTOTUNE=<autotune state>

Chooses whether this relay module should be automatically adjusted during a tuning cycle. <autotune state>=0 indicates the relay module should not be changed, and <autotune state>=1 indicates the relay module should be automatically adjusted.

OFFSETVAL=<offset value>

The amount of inductance, capacitance, or delay in the relay module when all of the adjustable components are turned off. This is to compensate for a minimum parasitic inductance, capacitance, or delay.

SETTLETIME=<time in ms>

This sets the amount of time after the relay change state command is issued over I2C that the tuner should wait for the state change to mechanically occur.

COMPVALUE=<component value 1>,<component value 2>,… <component value 16>

Set the values of the components at each relay. This is typically in nF for inductors, pF for capacitors, or 0.1 ns increments for delays. These values are separated by commas. Unused entries should be zero.

PORTBITS=<relay bit mask 1>,<relay bit mask 2>, … <relay bit mask 16>

Sets the bit masks corresponding to each relay for each component as specified in COMPVALUE. The values are in hexadecimal. Each bit mask should have only one nonzero bit. Unused entries should be zero. Generally the default values for the particular boards suffice and do not need to be changed.

SWITCHBITS=<switch bit mask 1>,<switch bit mask 2>

Sets the bit masks corresponding to the two switches. The bit masks are in hexadecimal. Generally the default values for the particular boards suffice and do not need to be changed.

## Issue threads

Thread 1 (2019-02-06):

Usage Questions...

BennehBoy, 2019-02-06:
Would this work with a CB Antenna (UK band)?  The little analogue SWR meters are pretty rubbish and prone to breaking...

profdc9, 2019-05-17:
This works as a CB SWR meter but it is quite a bit overkill for that, there are Arduino projects that would be simpler if you want a digital SWR meter.

Closed 2019-05-17.

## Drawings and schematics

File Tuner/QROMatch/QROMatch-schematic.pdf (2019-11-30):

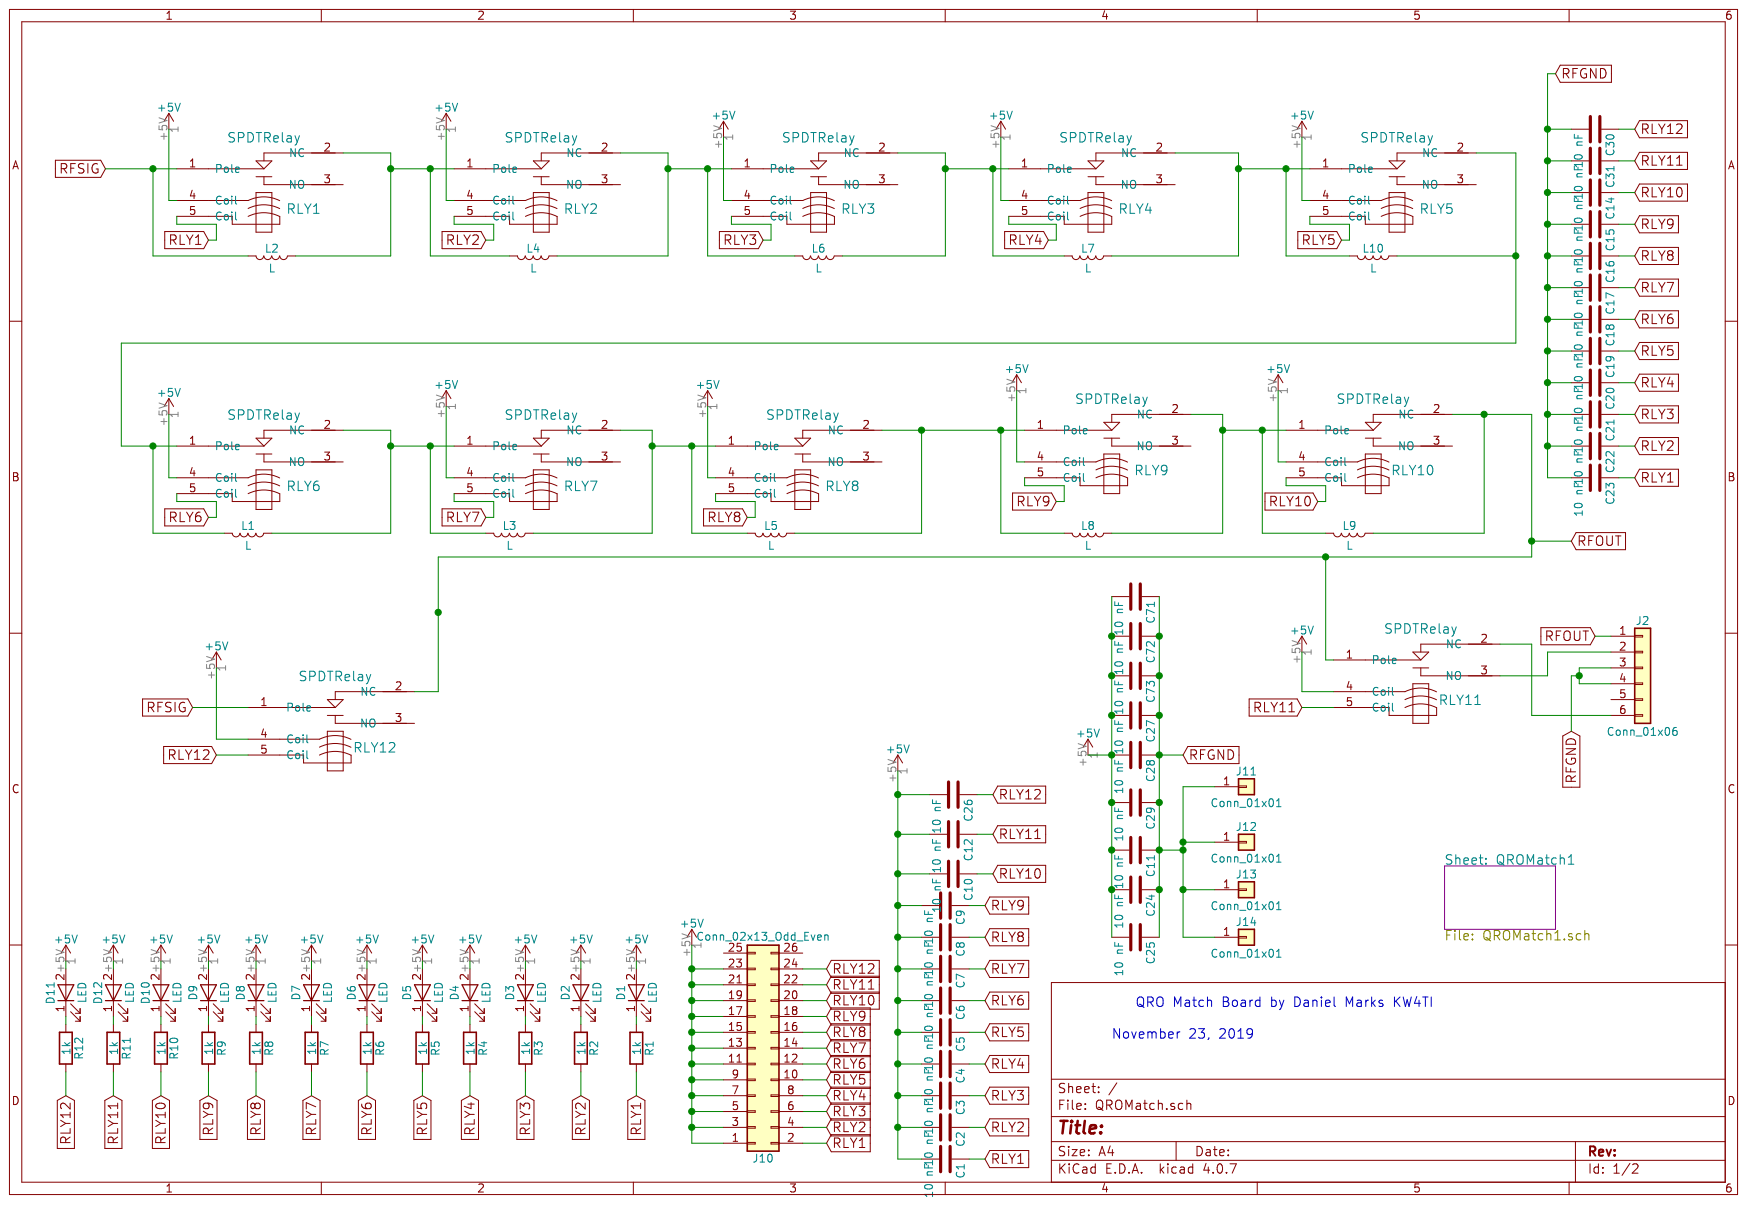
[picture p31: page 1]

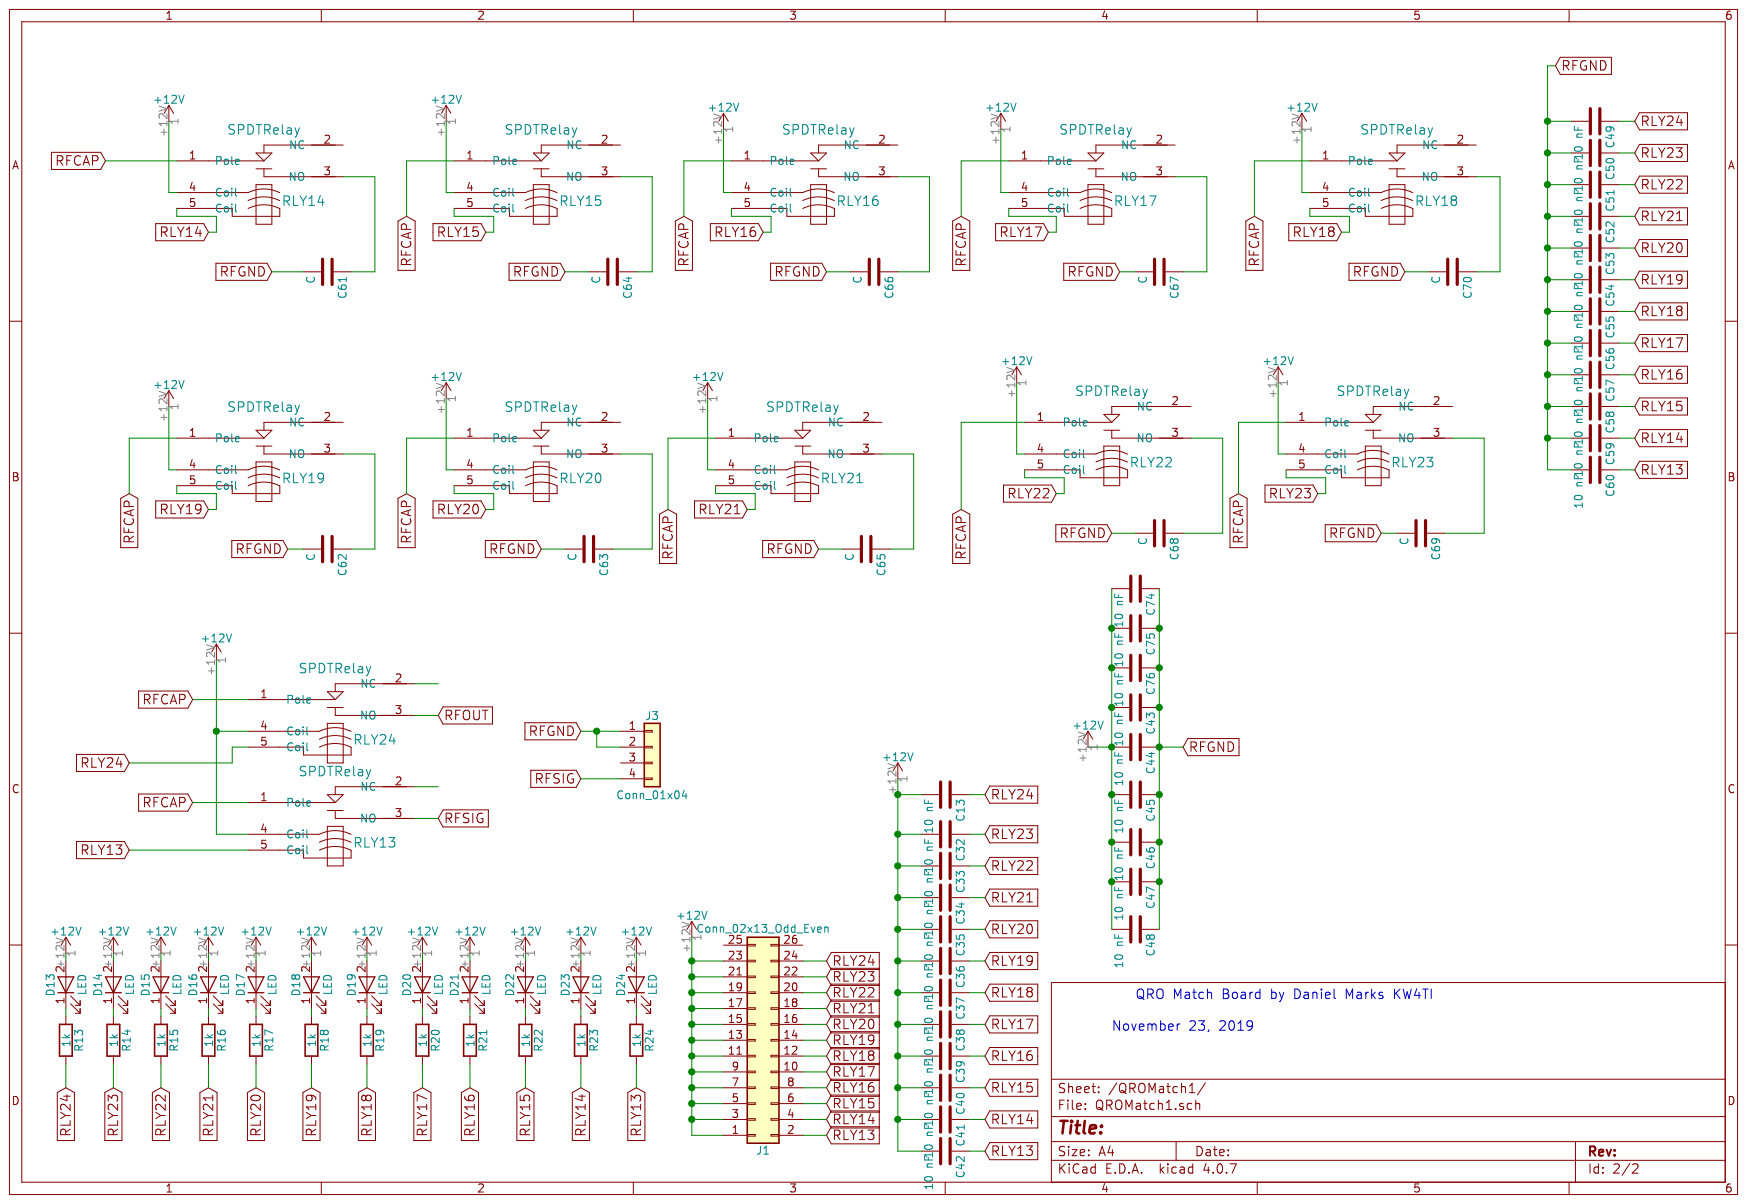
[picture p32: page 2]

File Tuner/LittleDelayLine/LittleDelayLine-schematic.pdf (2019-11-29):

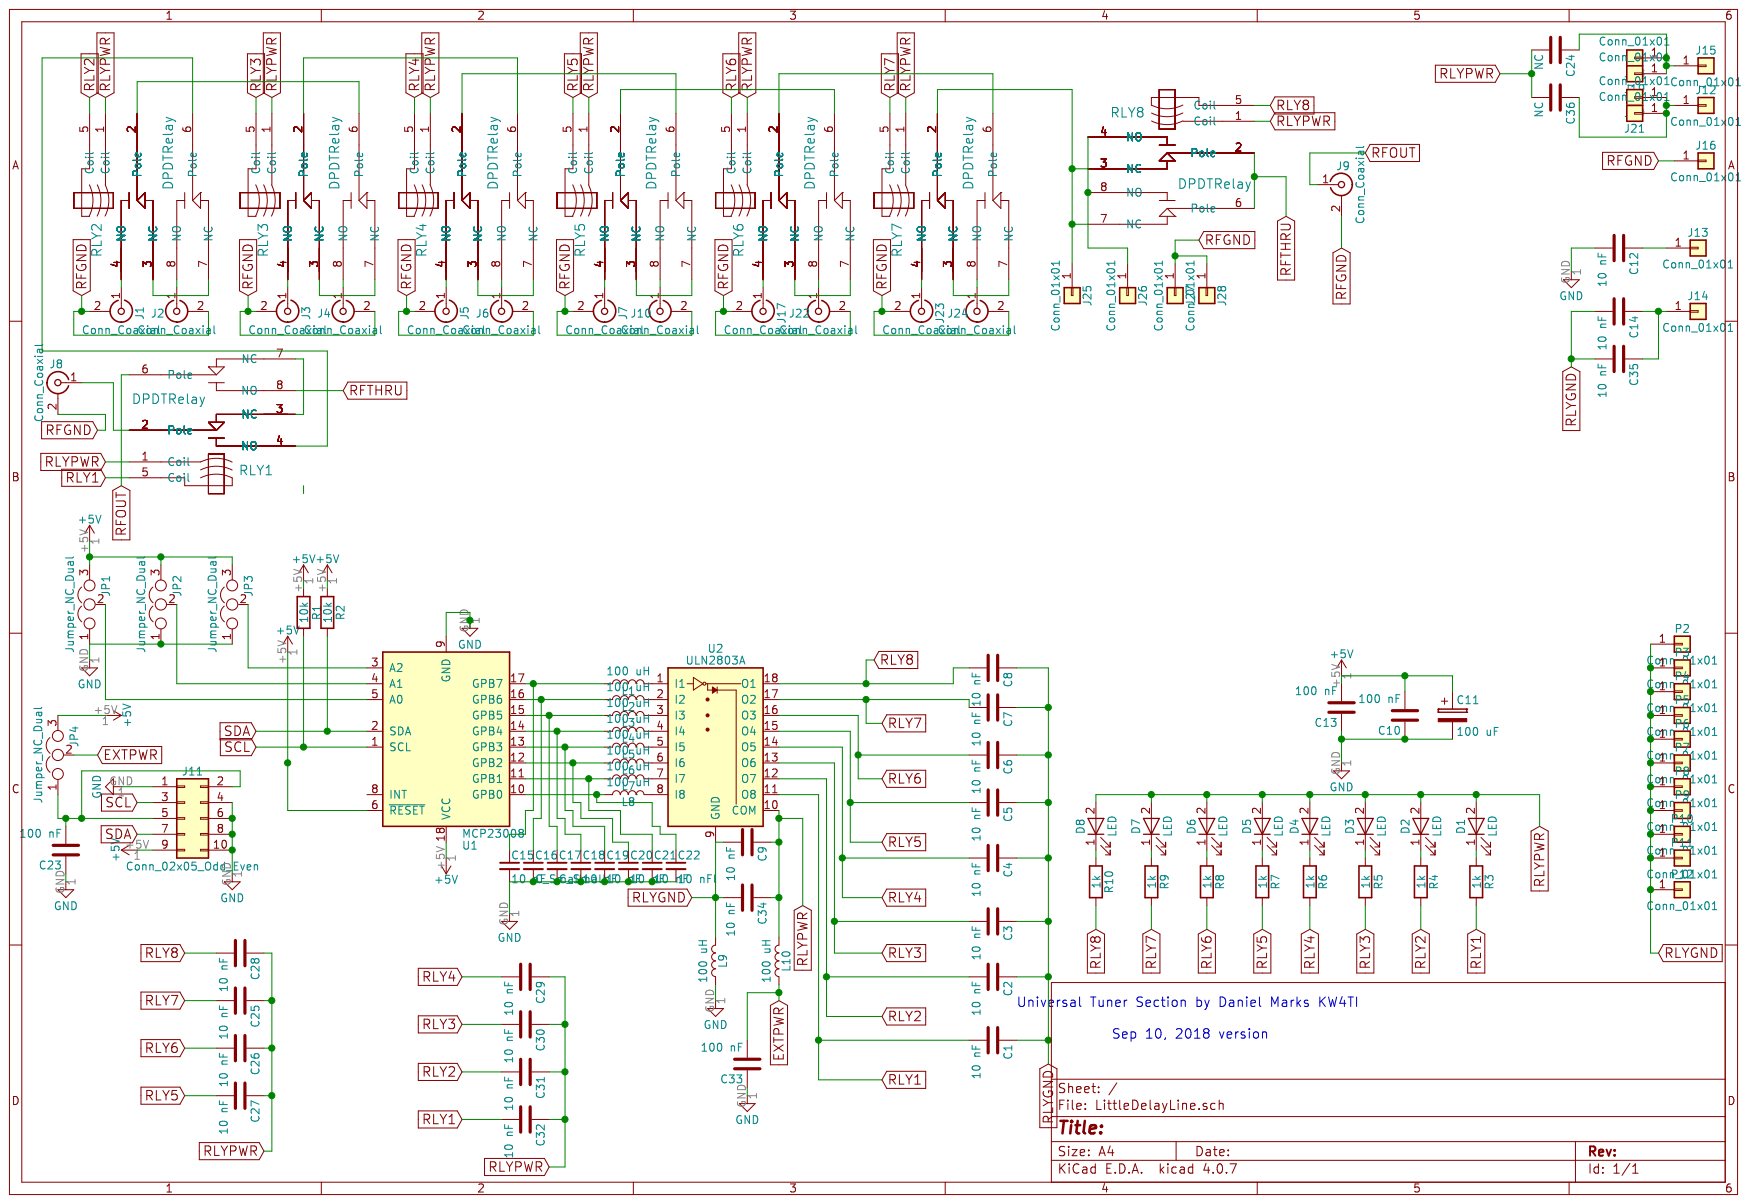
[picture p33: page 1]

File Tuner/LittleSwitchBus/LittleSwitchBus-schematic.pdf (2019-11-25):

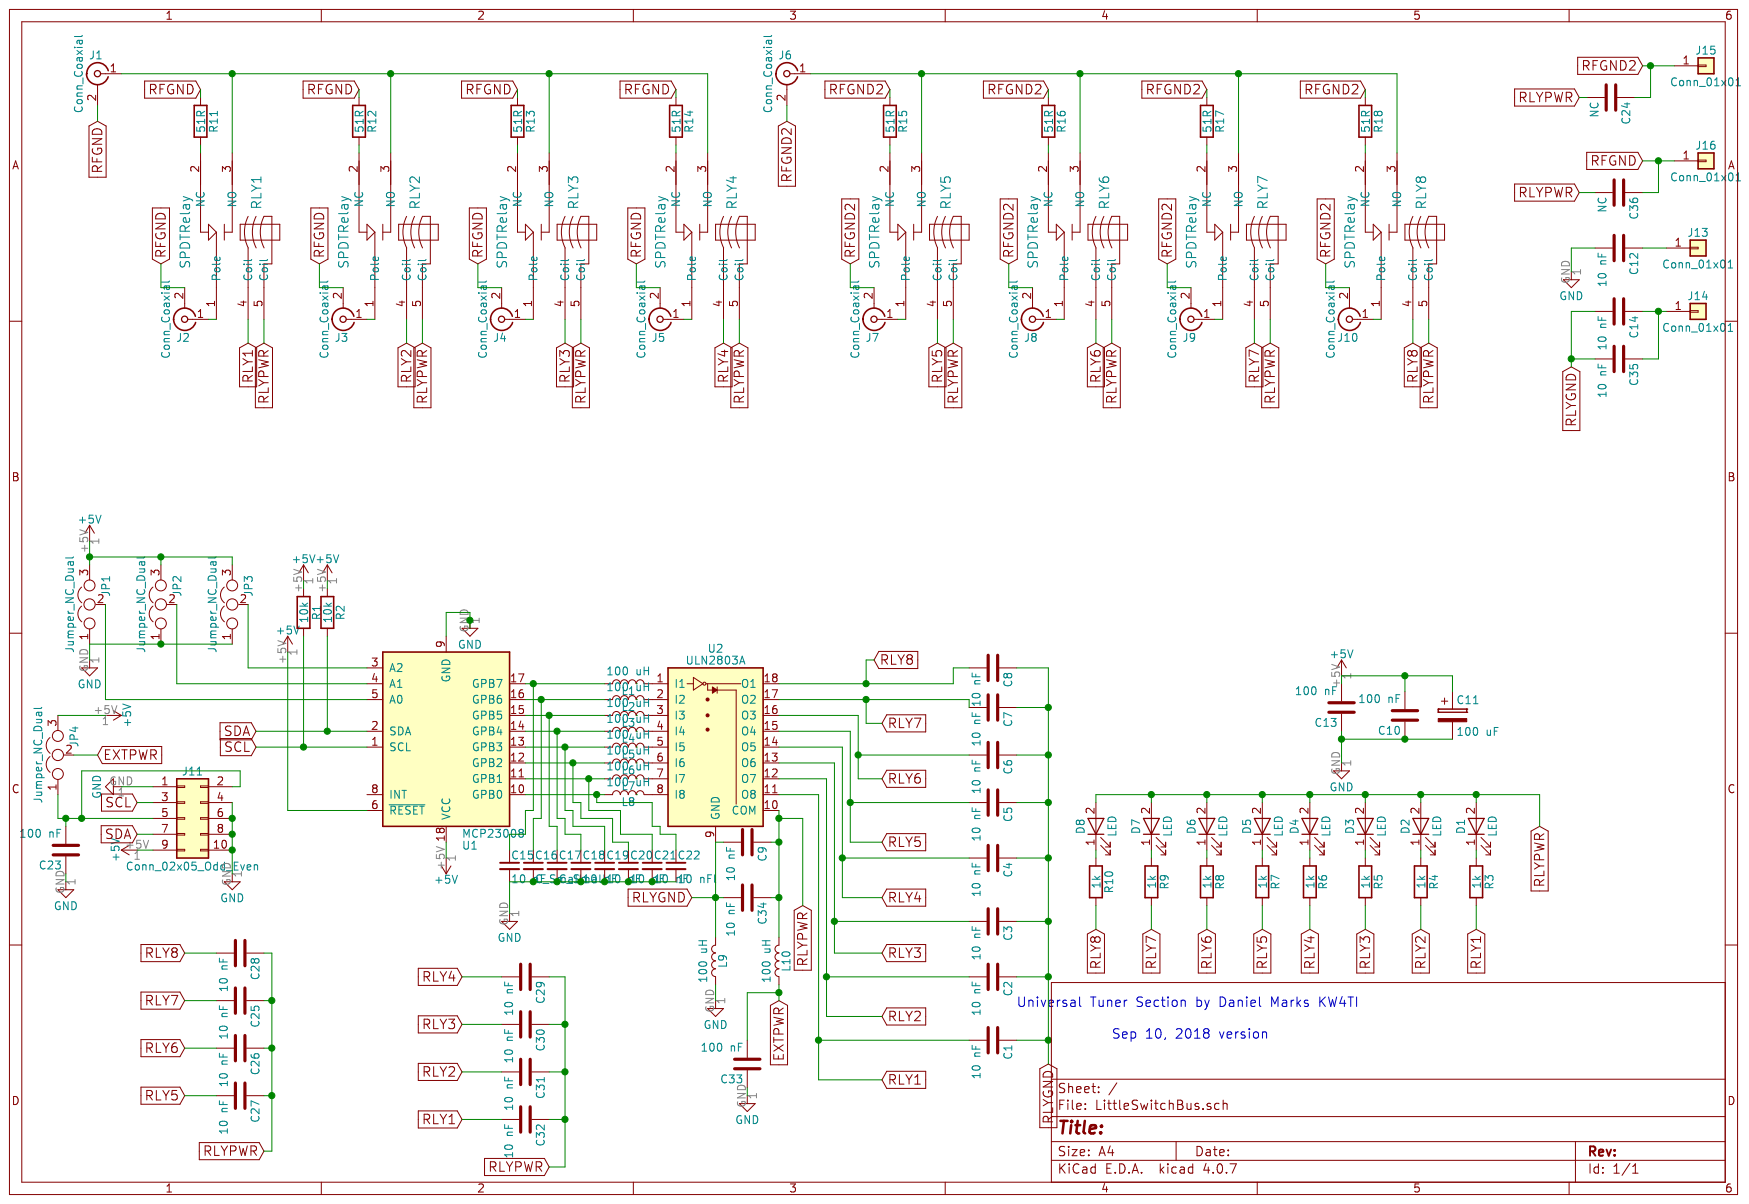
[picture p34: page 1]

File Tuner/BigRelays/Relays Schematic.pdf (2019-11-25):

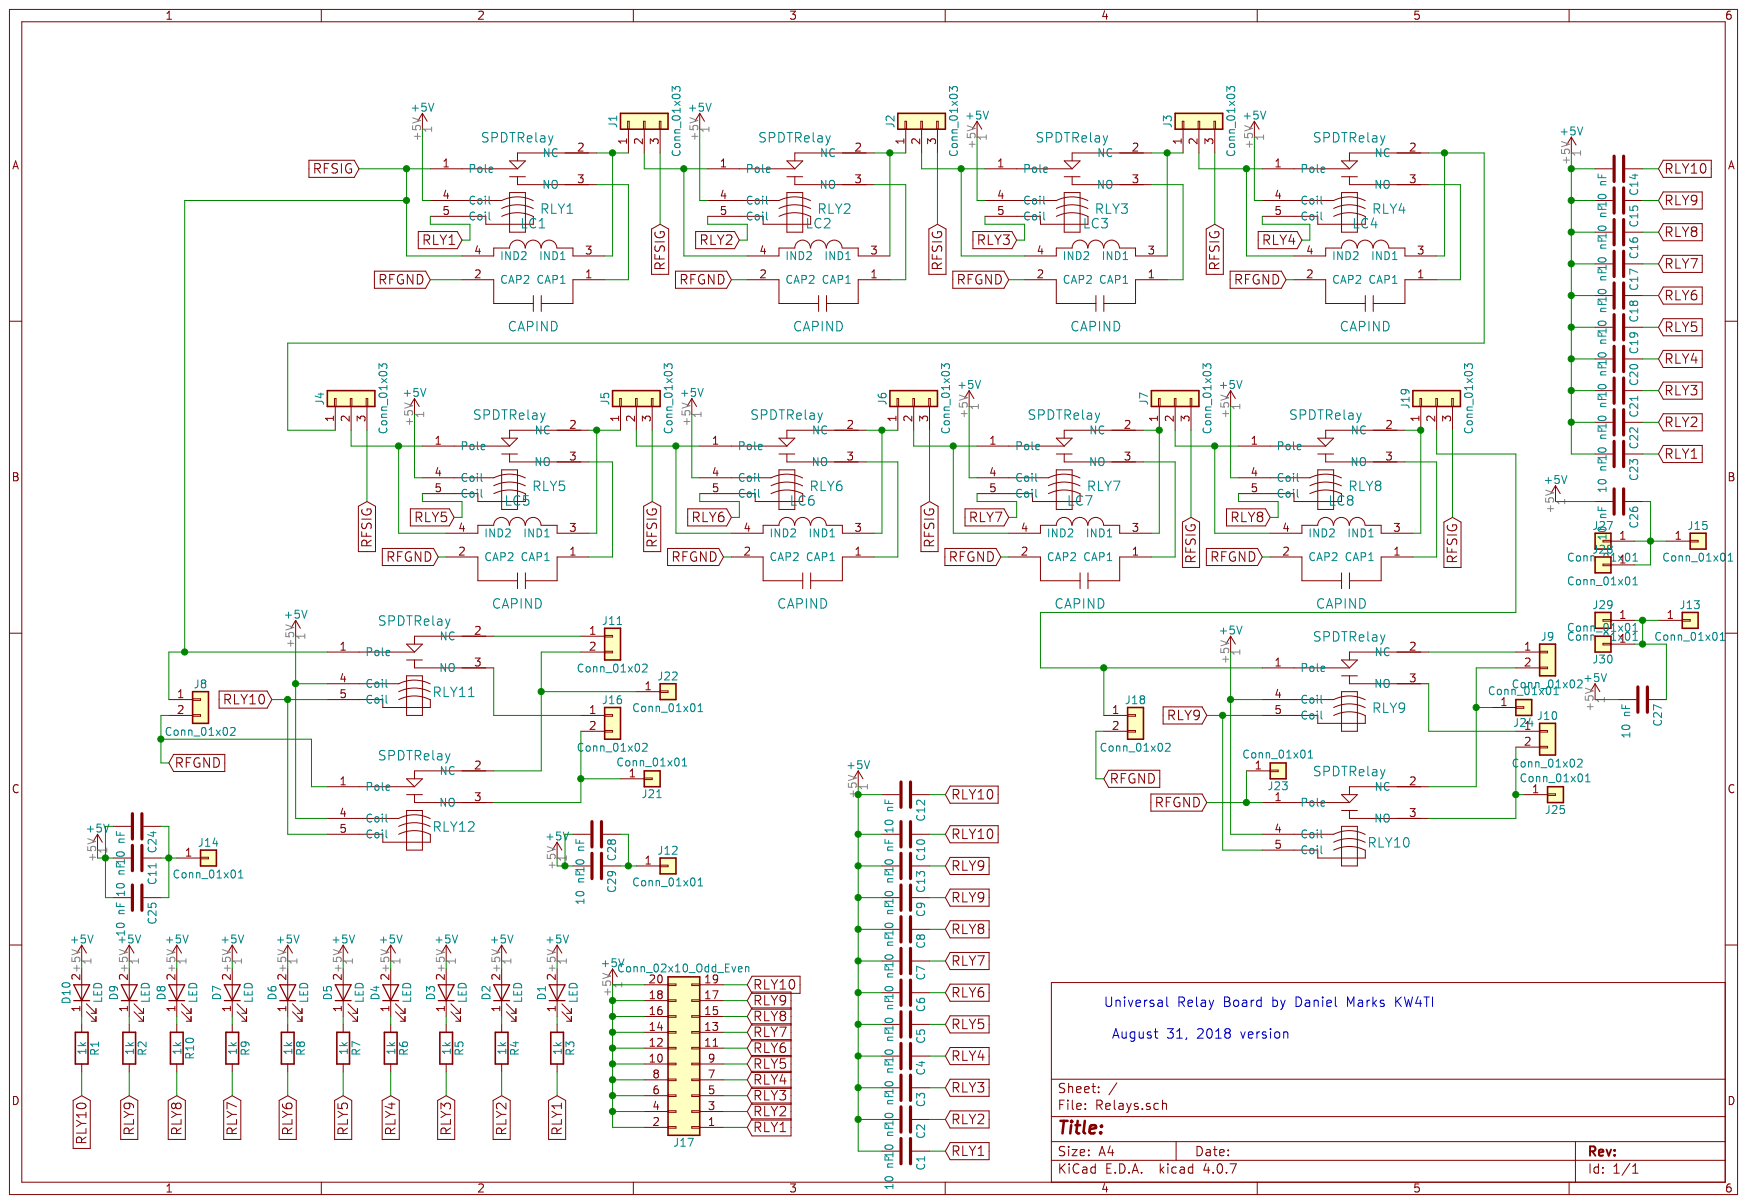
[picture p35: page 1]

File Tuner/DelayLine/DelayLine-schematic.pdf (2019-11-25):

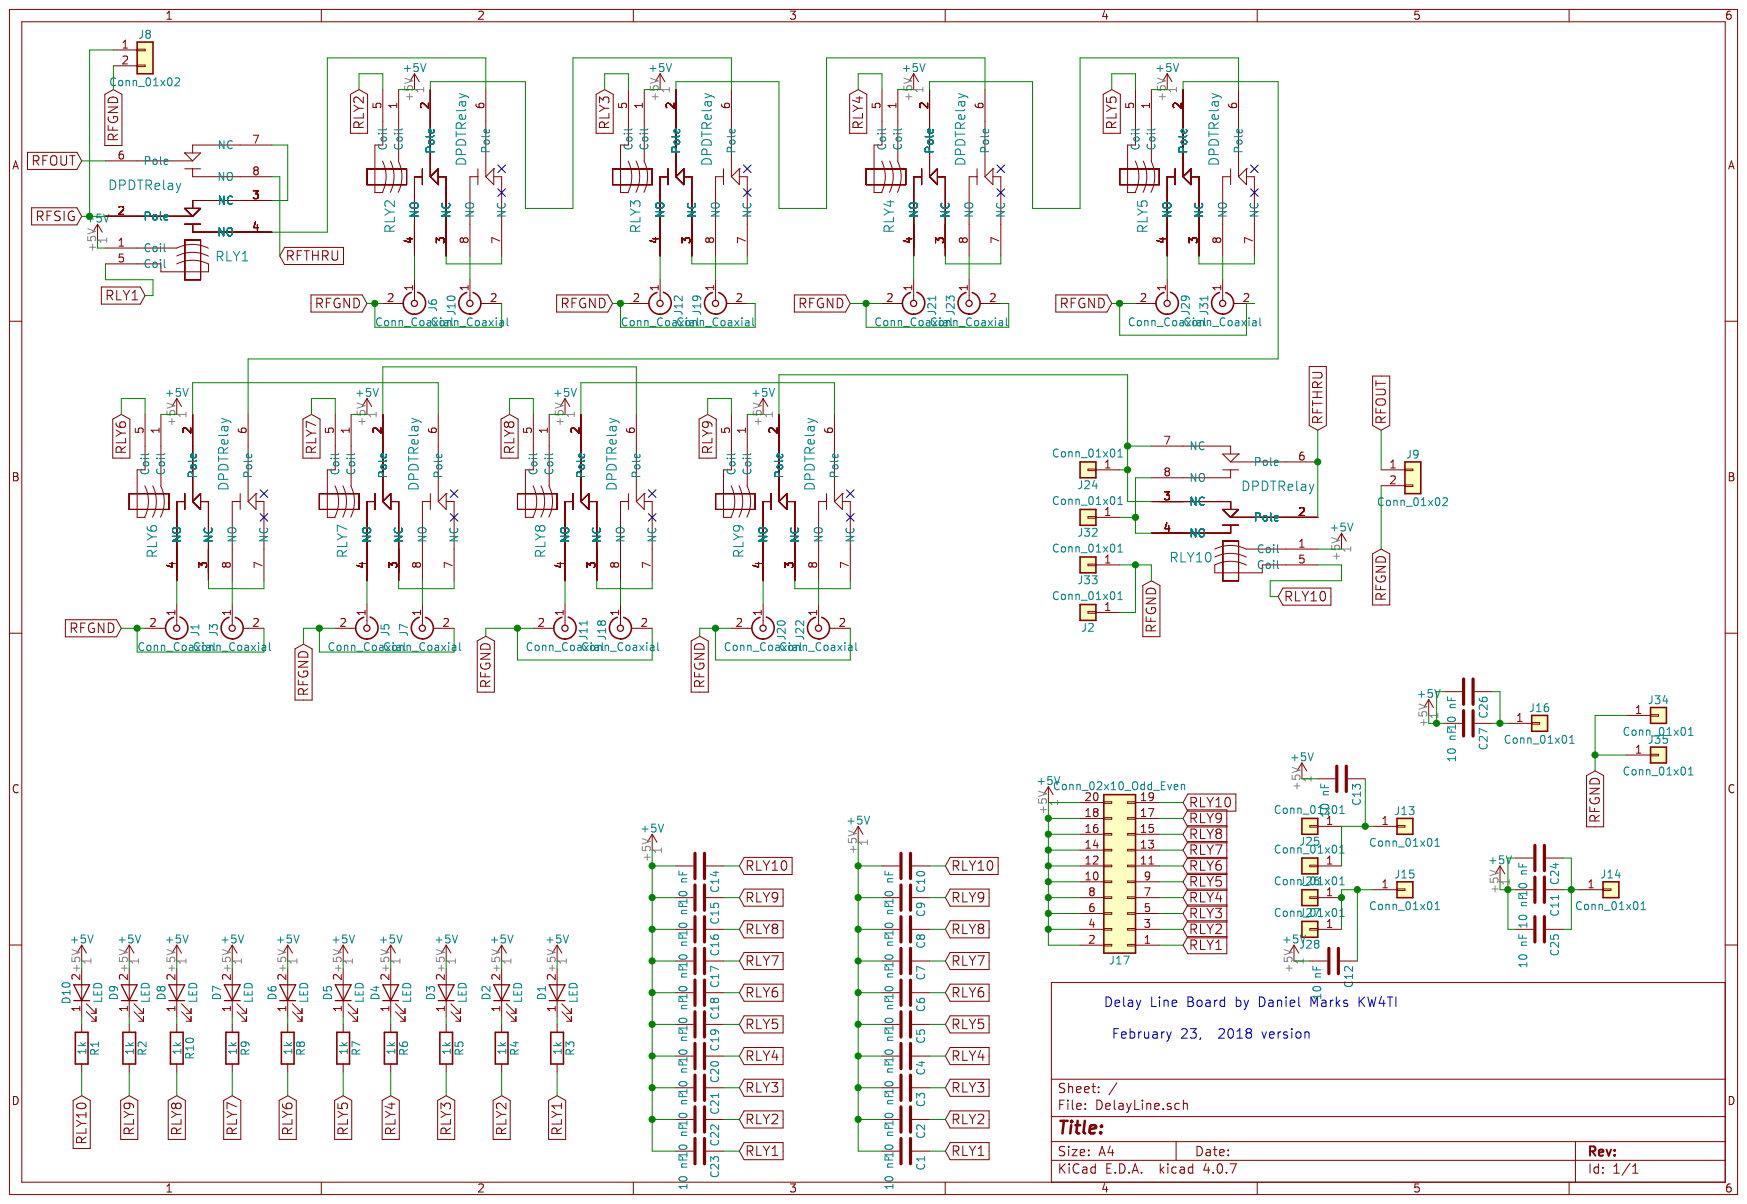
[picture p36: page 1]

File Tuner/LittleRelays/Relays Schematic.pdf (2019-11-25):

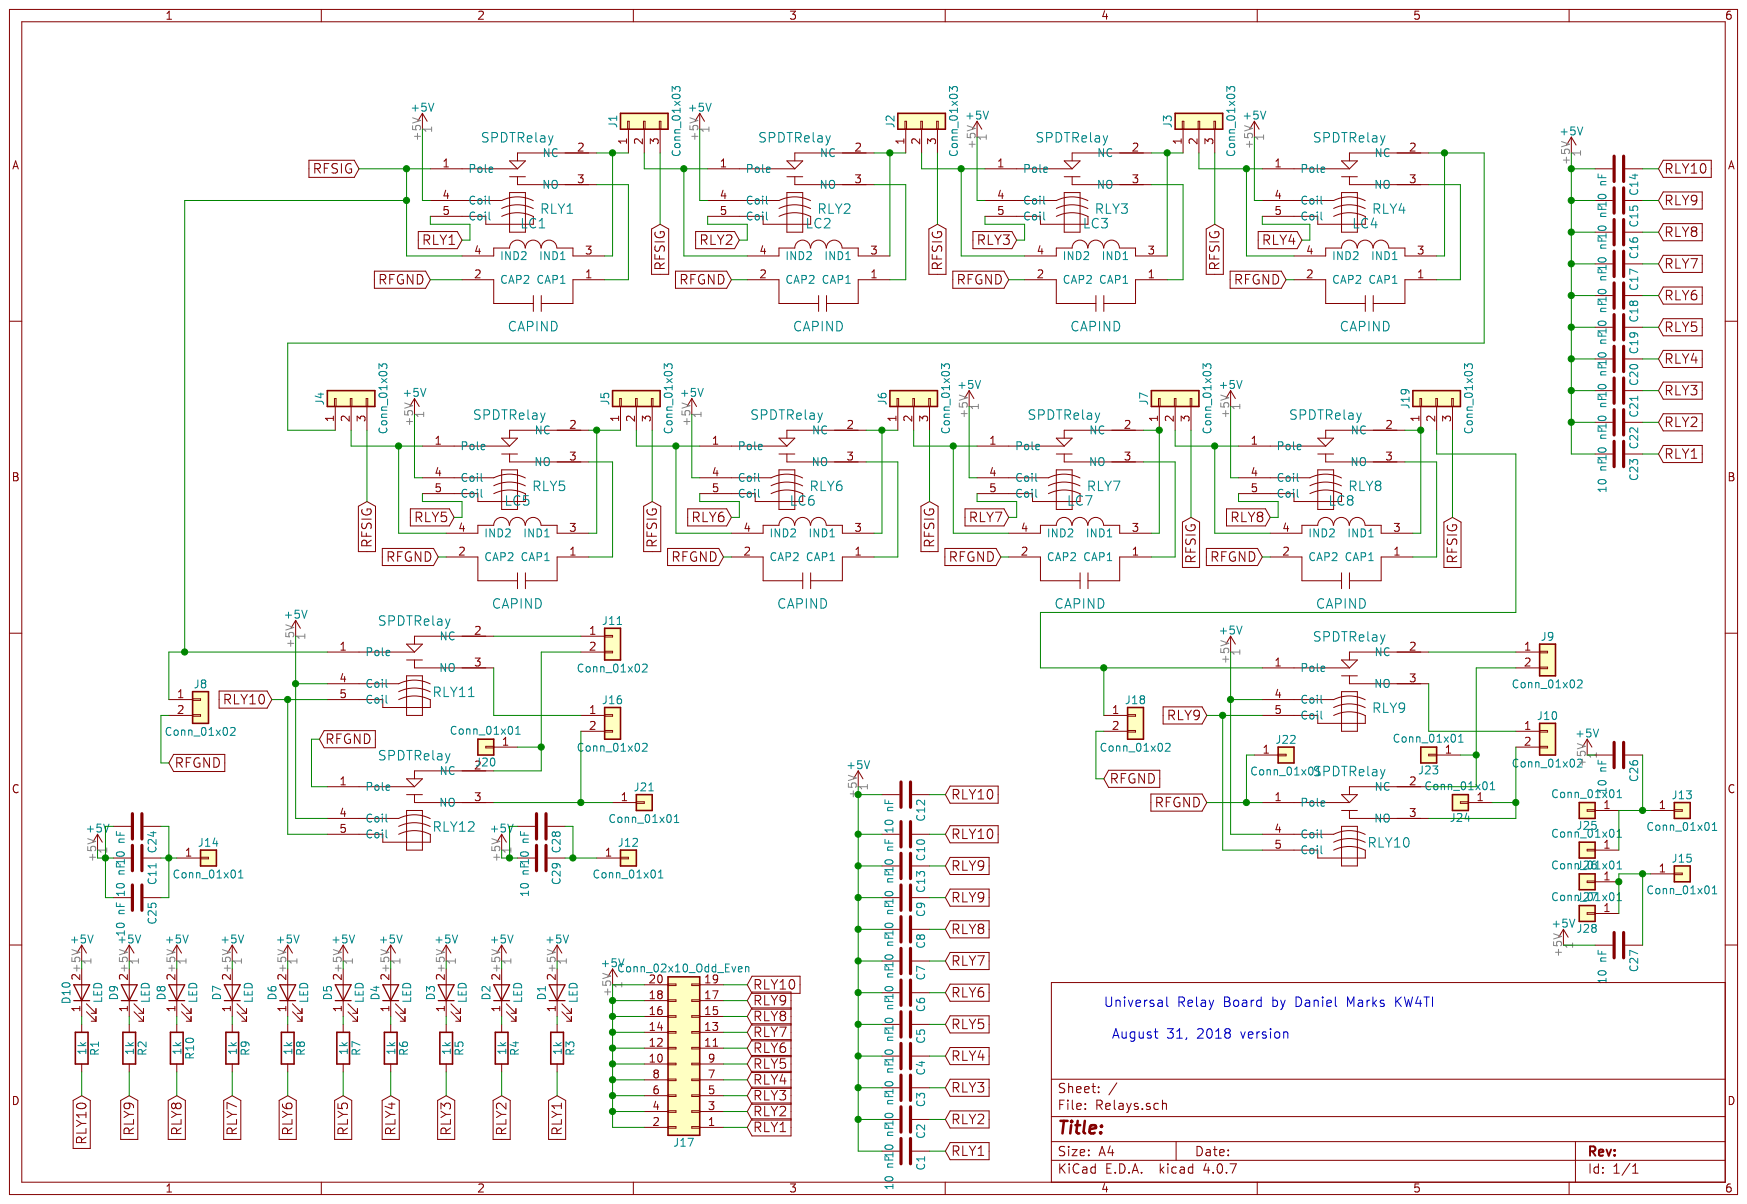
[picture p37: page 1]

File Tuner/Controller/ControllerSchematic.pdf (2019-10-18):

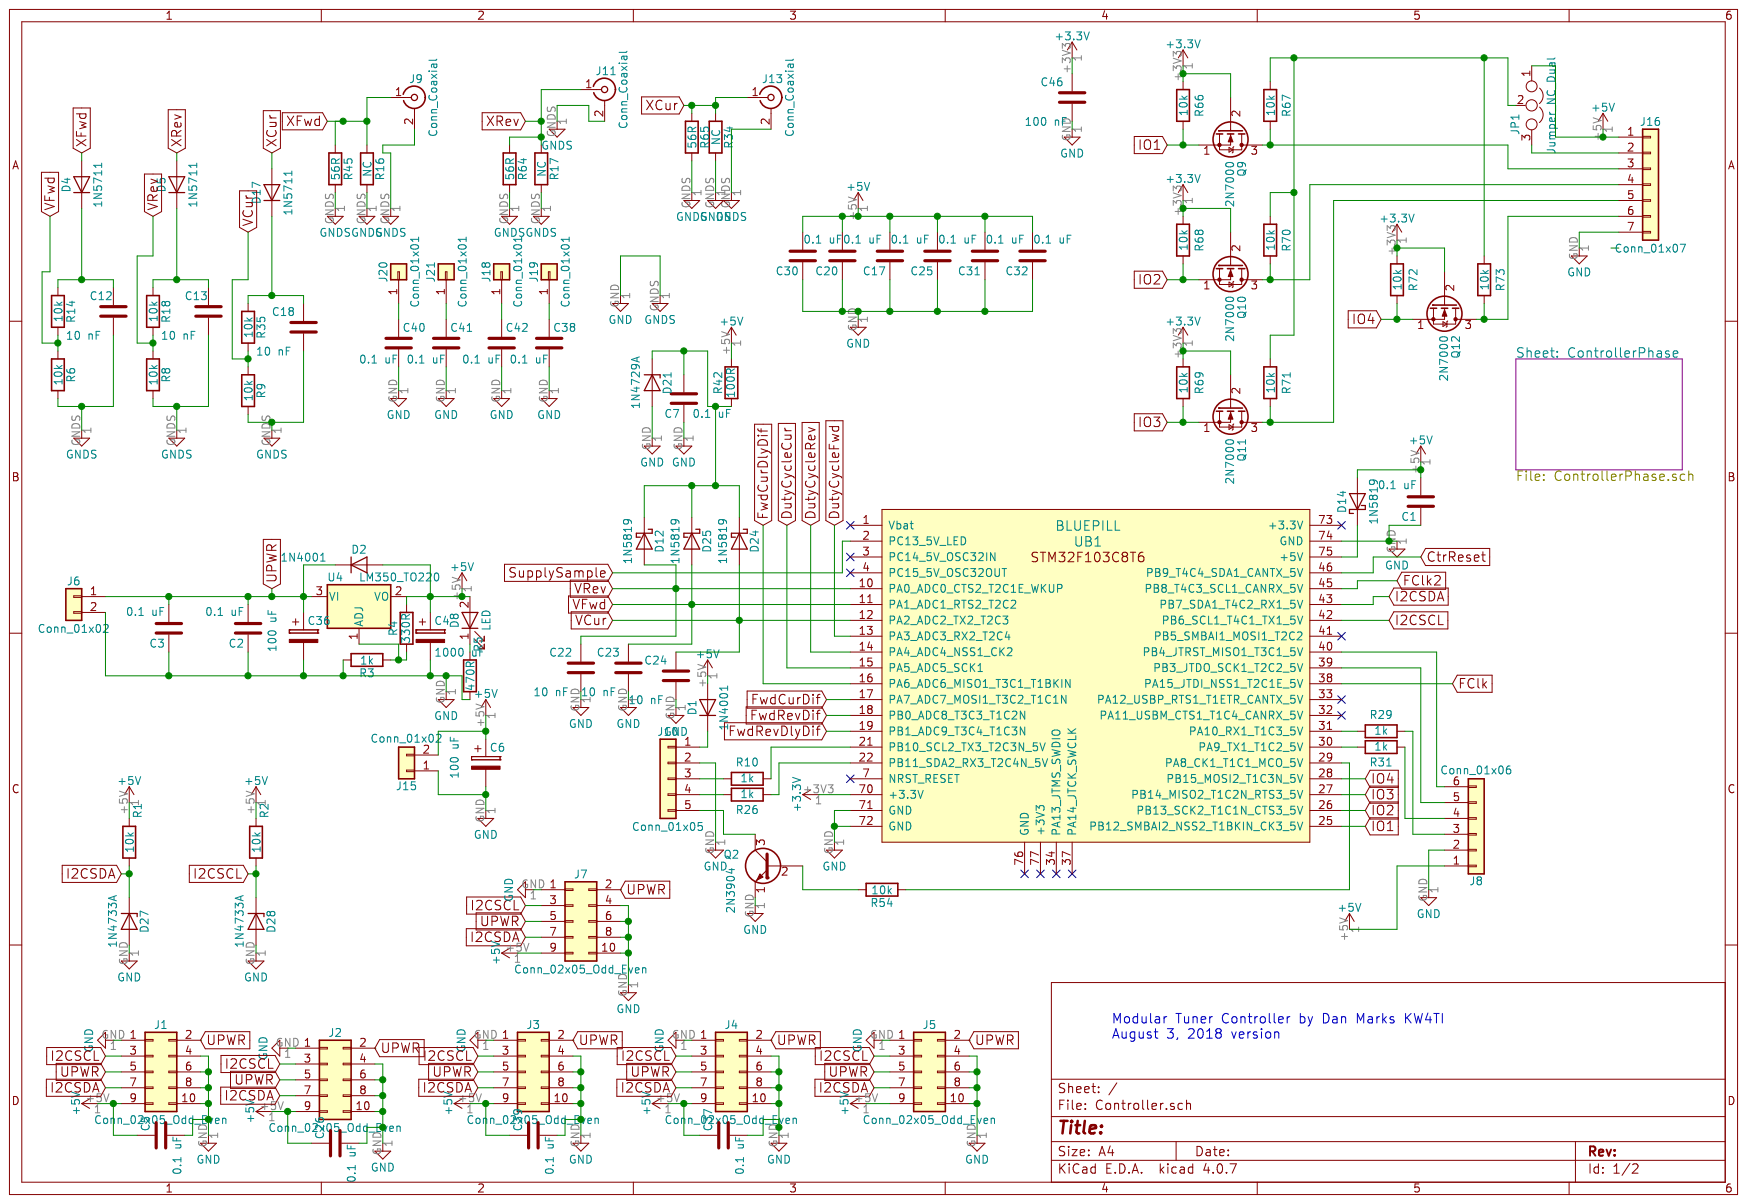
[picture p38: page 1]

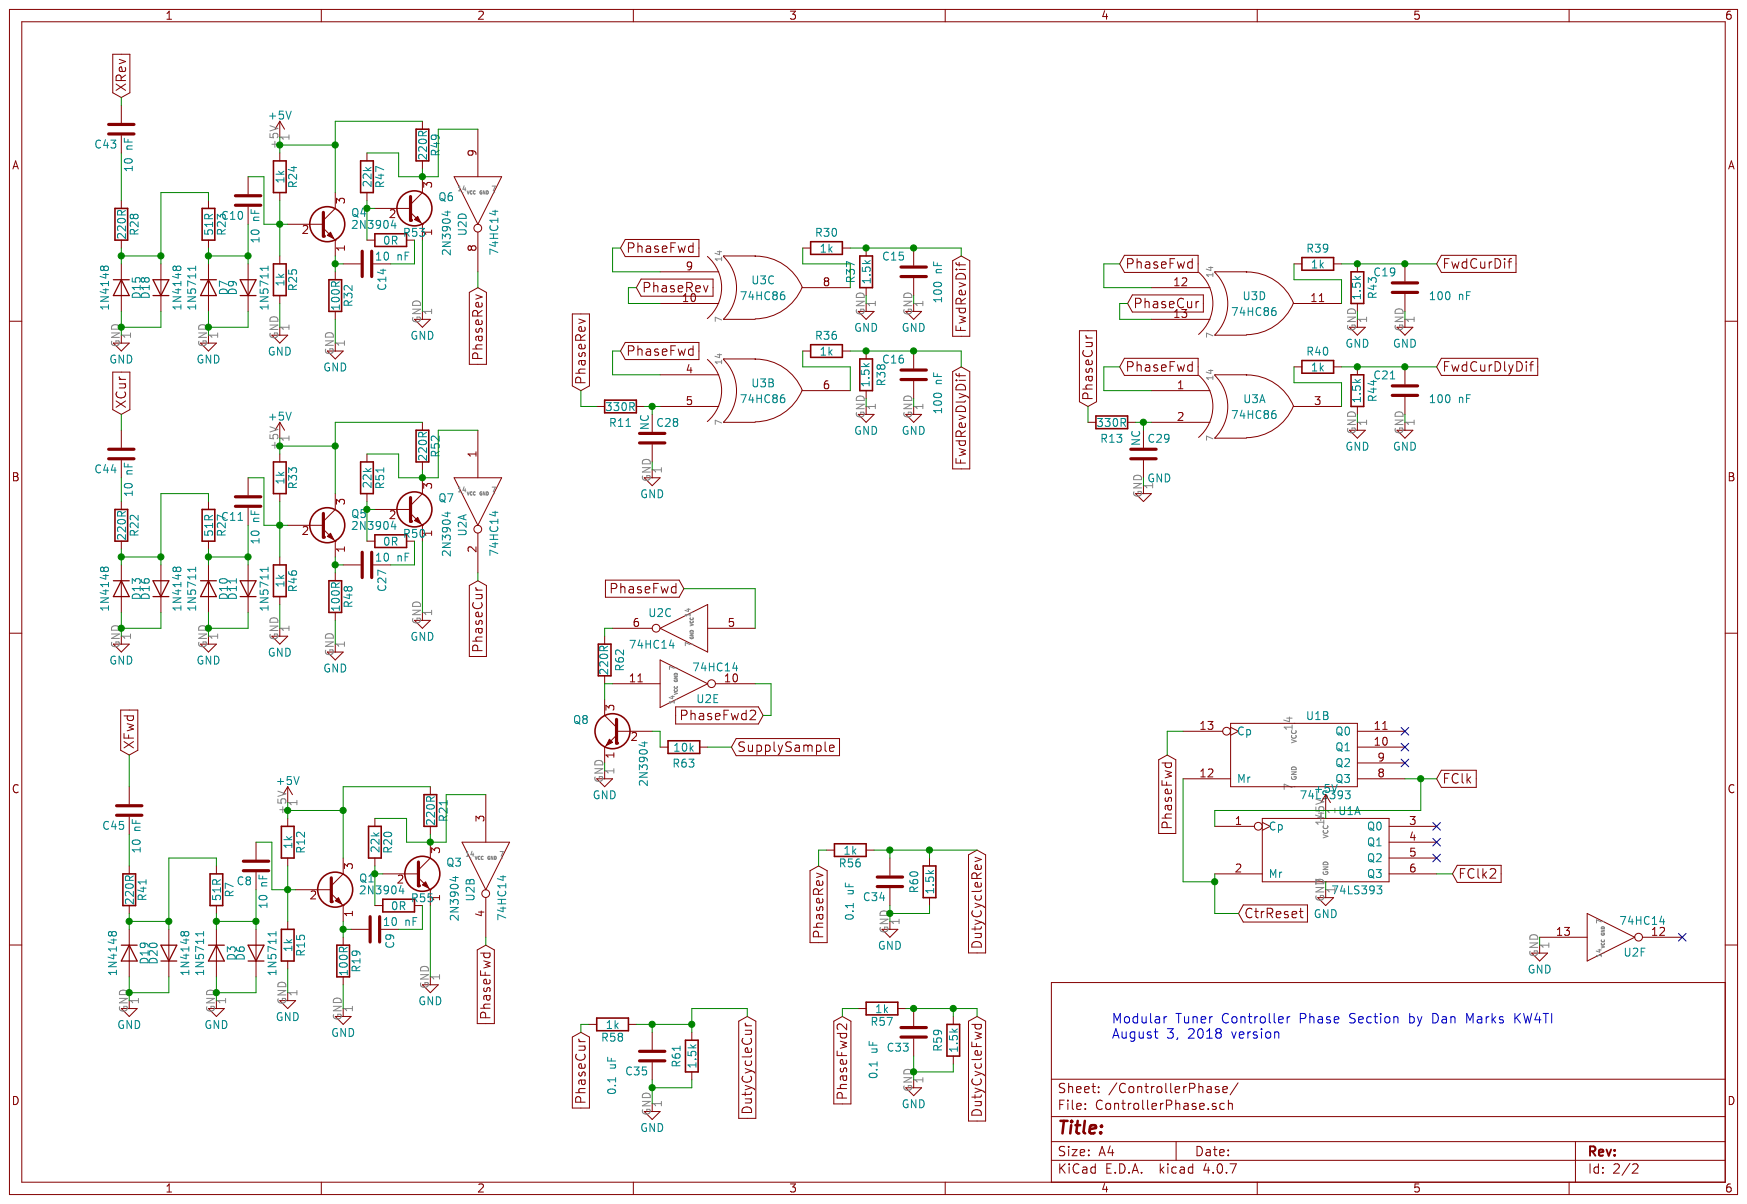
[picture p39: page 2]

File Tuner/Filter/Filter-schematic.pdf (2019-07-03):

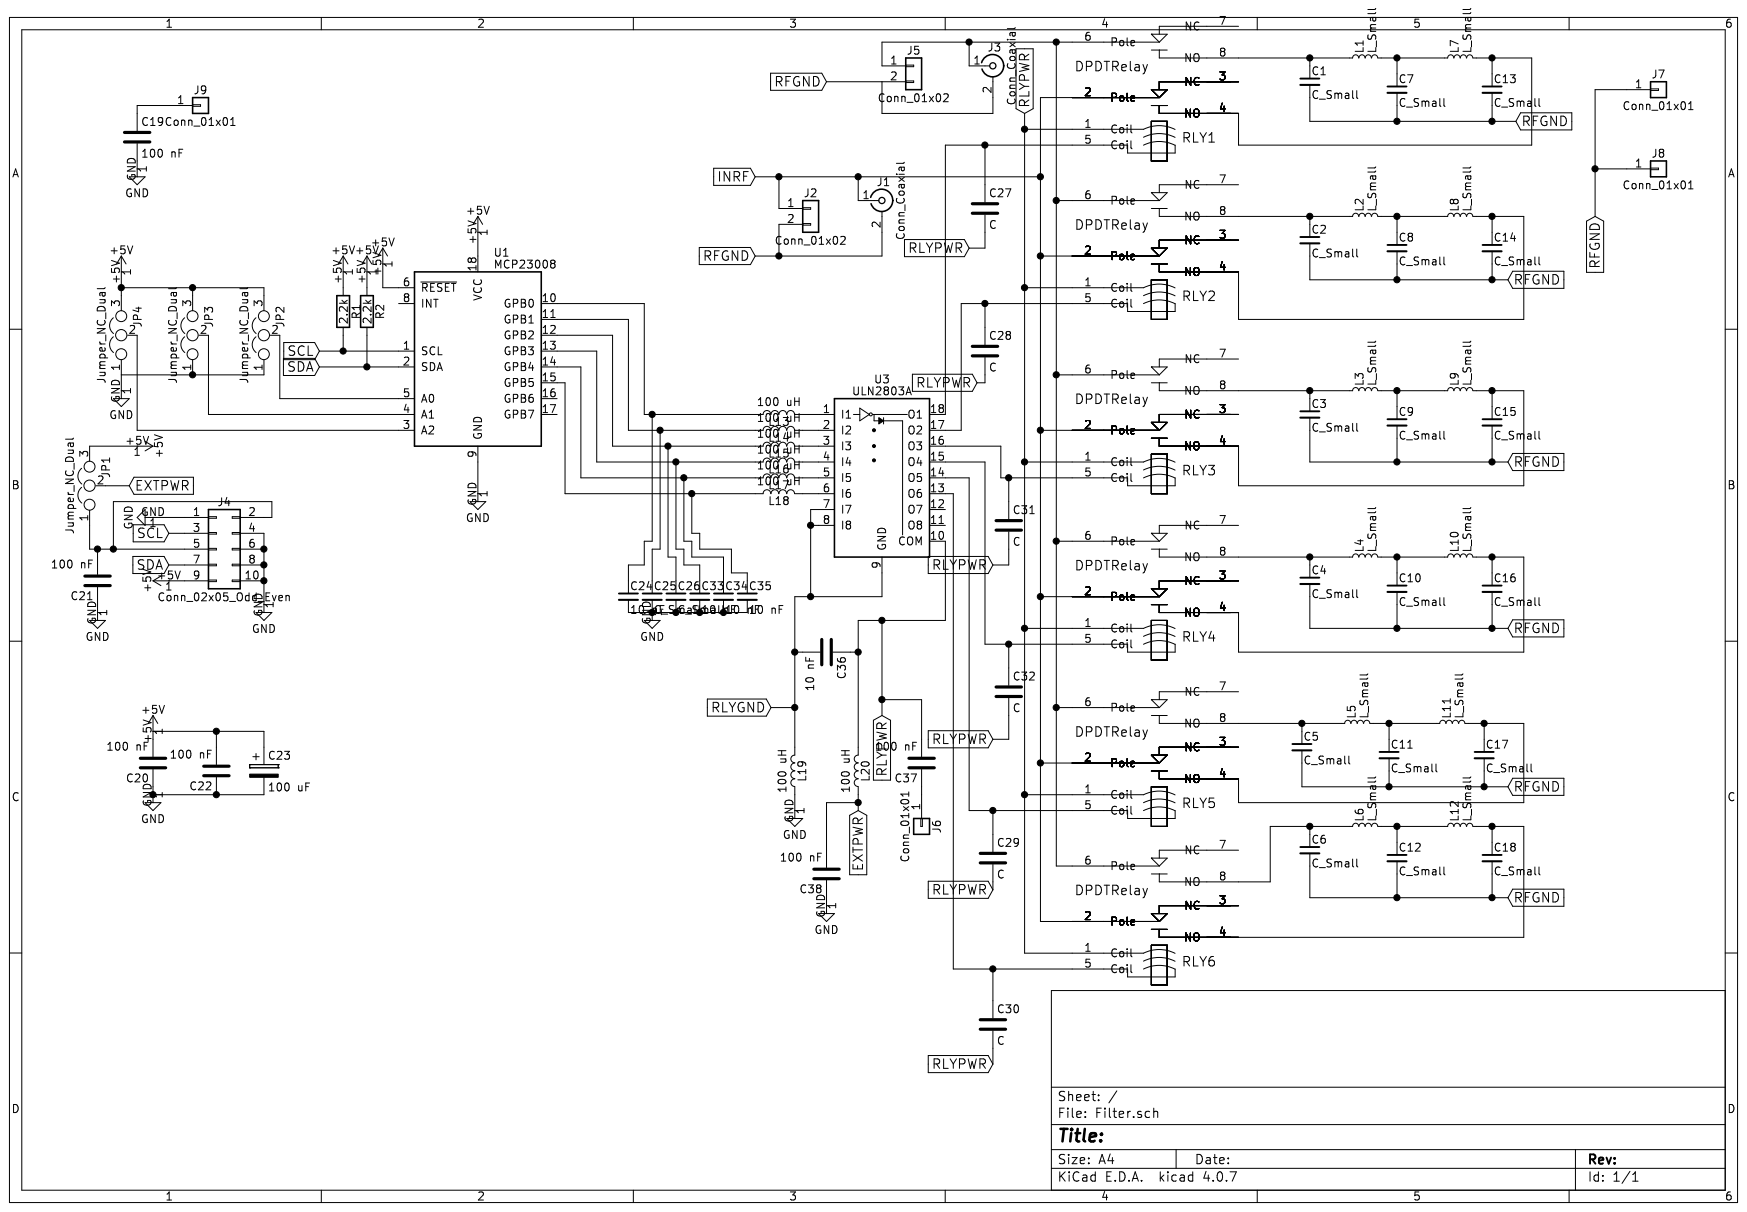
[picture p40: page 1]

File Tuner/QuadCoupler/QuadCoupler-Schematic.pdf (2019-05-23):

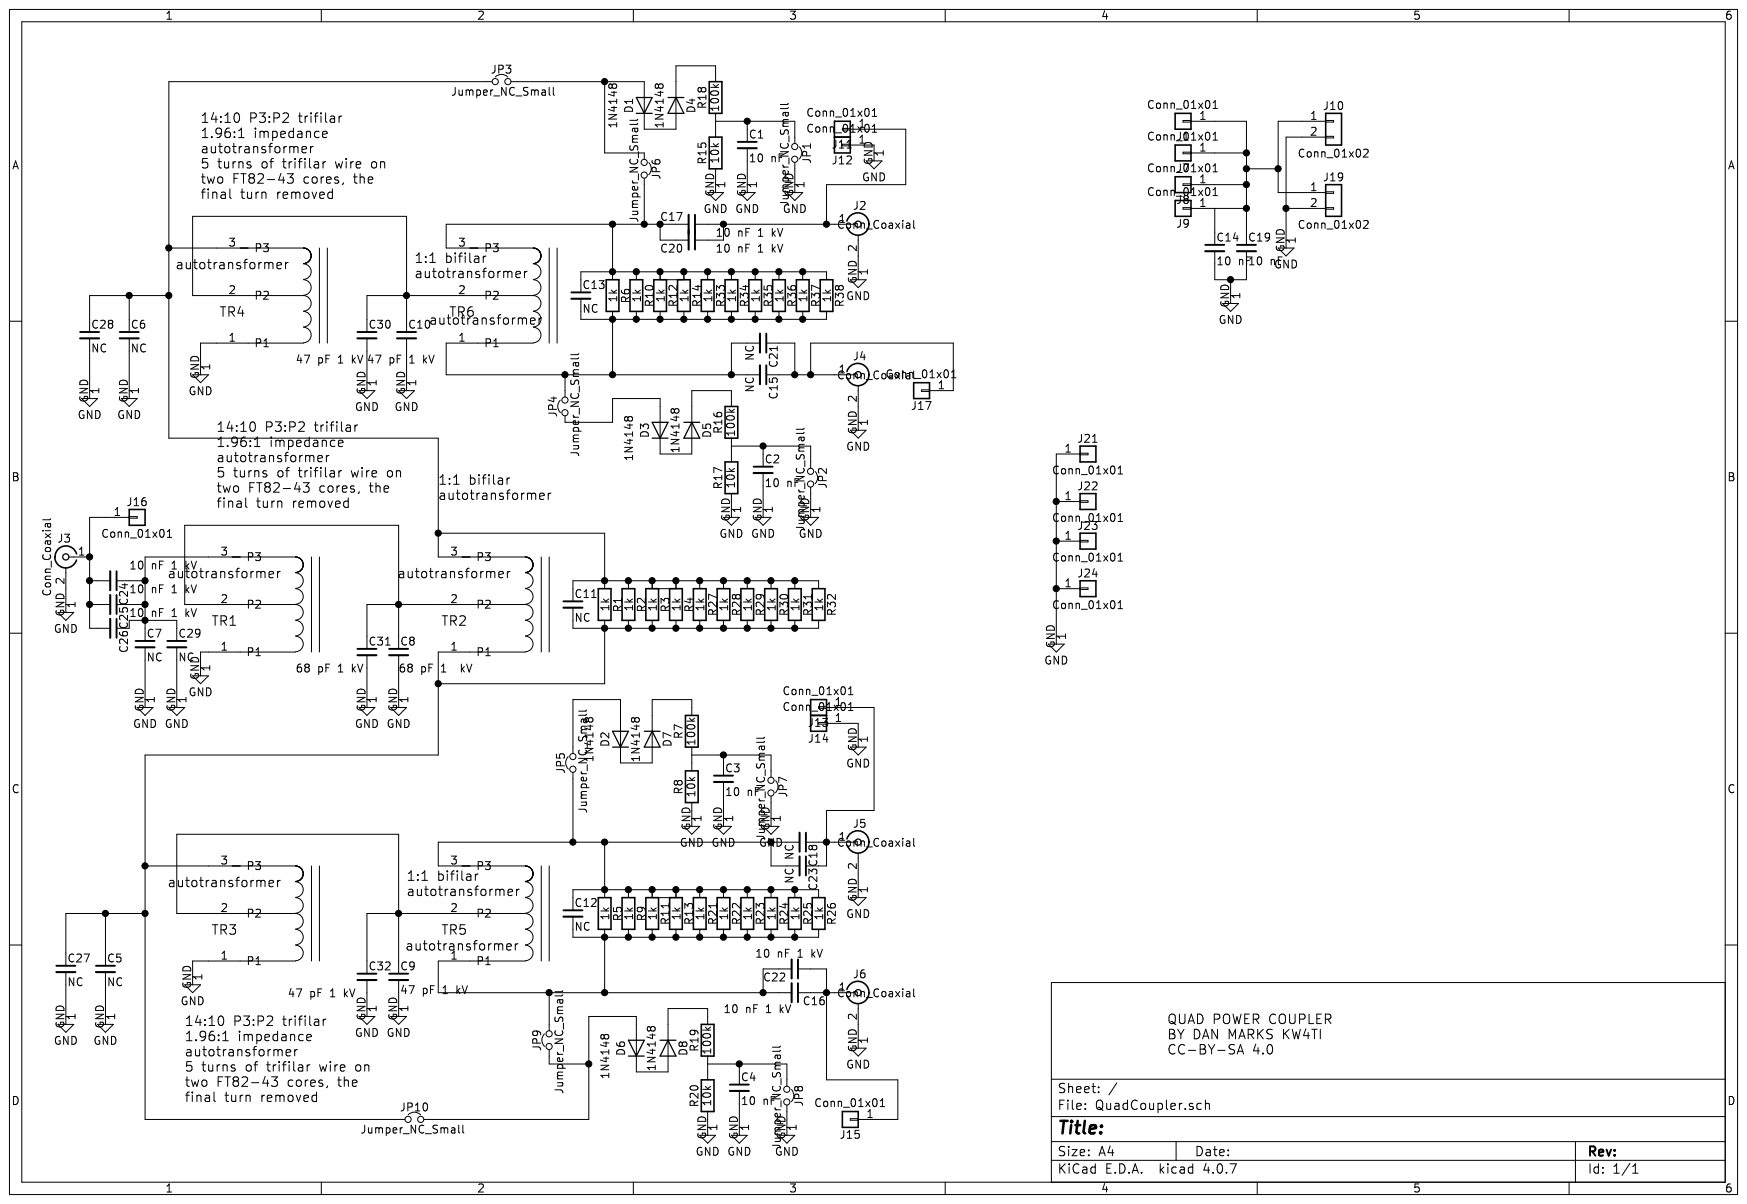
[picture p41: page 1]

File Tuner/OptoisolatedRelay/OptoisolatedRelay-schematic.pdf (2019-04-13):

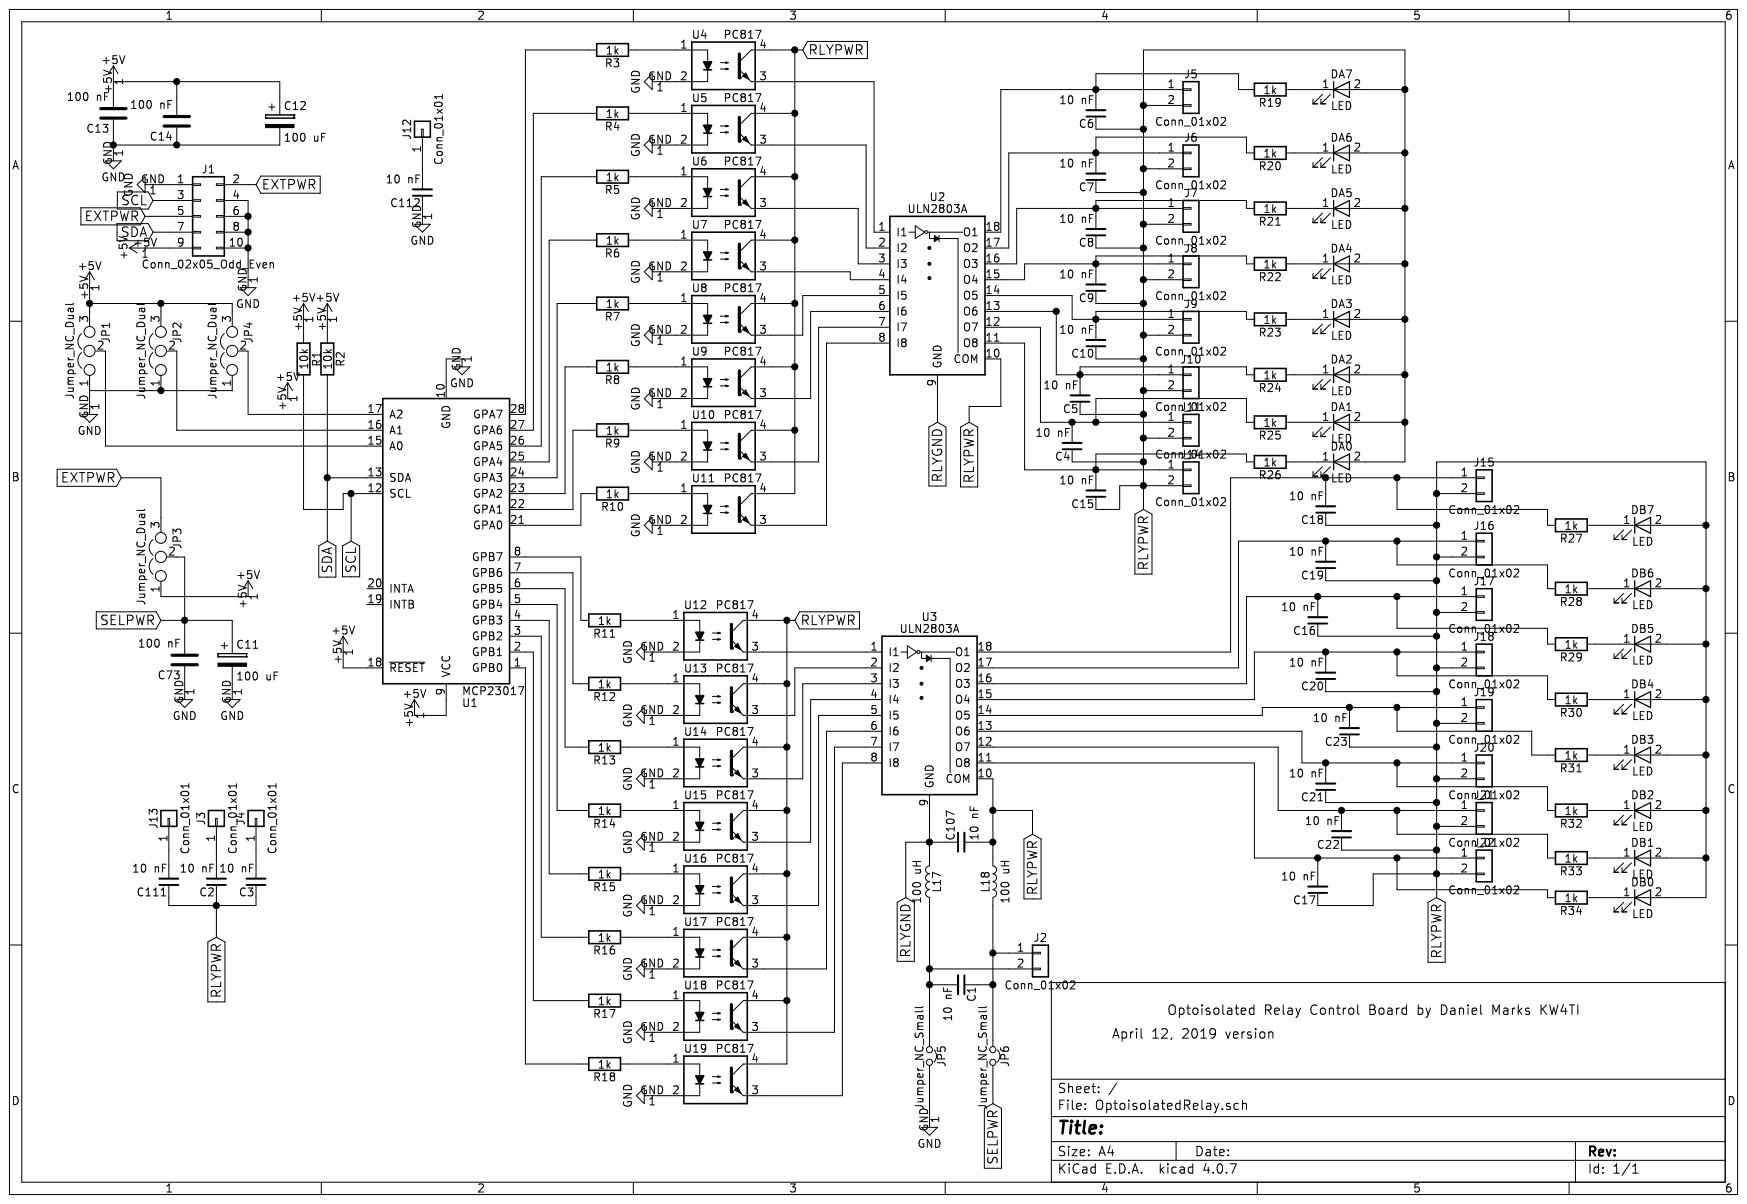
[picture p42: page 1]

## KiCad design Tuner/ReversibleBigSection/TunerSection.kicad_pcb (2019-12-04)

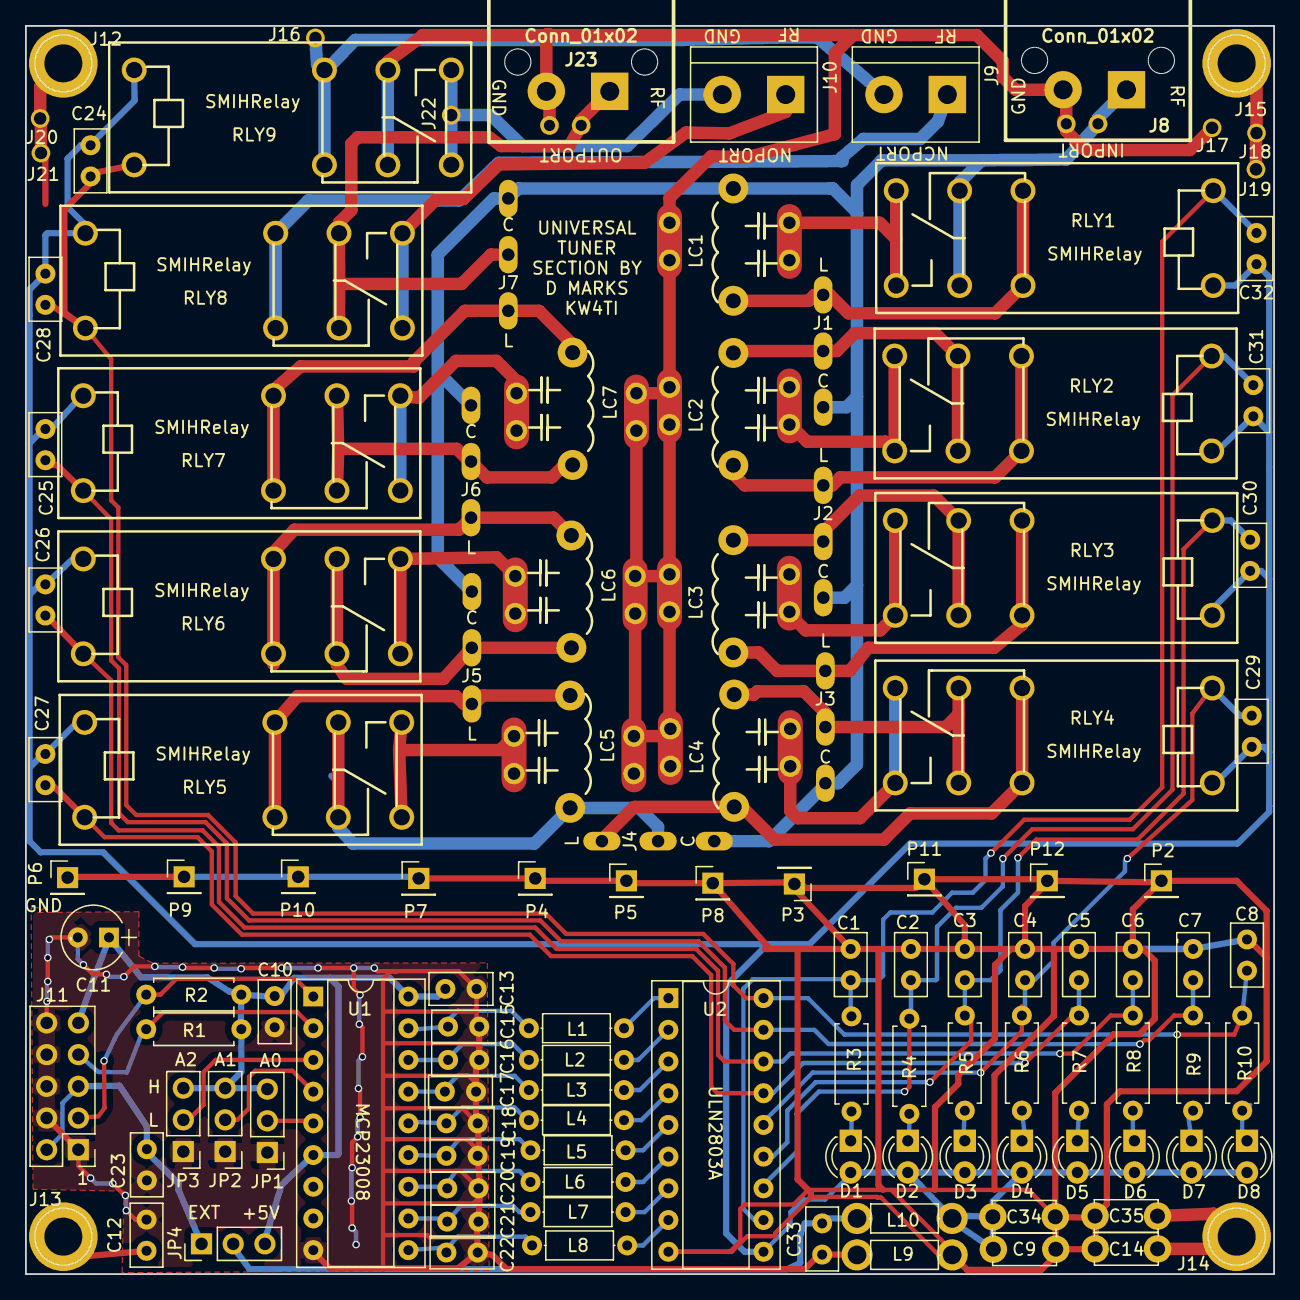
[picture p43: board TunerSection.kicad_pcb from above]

Board: 2 copper layers, 100.0 x 100.0 mm, 119 parts (0 on the bottom side), 74 nets.

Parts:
C1, C2, C3, C4, C5, C6, C7, C8, C12, C15, C18, C19, C20, C21, C24, C25, C26, C27, C28, C29, C30, C31, C32: 10 nF; C_Disc_D5.0mm_W2.5mm_P2.50mm
C9, C14, C34, C35: 10 nF; C_Disc_D5.0mm_W2.5mm_P5.00mm
C10, C13, C23, C33: 100 nF; C_Disc_D5.0mm_W2.5mm_P2.50mm
C11: 100 uF; CP_Radial_Tantal_D5.0mm_P2.50mm
C16, C17: C_Small; C_Disc_D5.0mm_W2.5mm_P2.50mm
C22: 10 nFl; C_Disc_D5.0mm_W2.5mm_P2.50mm
D1, D2, D3, D4, D5, D6, D7, D8: LED; LED_D3.0mm
J1, J2, J3, J4, J5, J6, J7: Conn_01x03; ThreeJumperPt
J8, J23: Conn_01x02; bnc_90_1-1337543-0_pad_combo
J9, J10: Conn_01x02; TerminalBlock_bornier-2_P5.08mm
J11: Conn_02x05_Odd_Even; Pin_Header_Straight_2x05_Pitch2.54mm
J12, J13, J14, J15: Conn_01x01; 1pin
J16, J17, J18, J19, J20, J21, J22: Conn_01x01; SOLDERJUMPER
JP1, JP2, JP3, JP4: Jumper_NC_Dual; Pin_Header_Straight_1x03_Pitch2.54mm
L1, L2, L3, L4, L5, L6, L7, L8, L9, L10: 100 uH; L_Axial_L5.3mm_D2.2mm_P7.62mm_Horizontal_Vishay_IM-1
LC1, LC2, LC3, LC4, LC5, LC6, LC7: CAPIND; MultiCAPIND
P2, P3, P4, P5, P6, P7, P8, P9, P10, P11, P12: Conn_01x01; Pin_Header_Straight_1x01_Pitch2.54mm
R1, R2: 2.2k; R_Axial_DIN0207_L6.3mm_D2.5mm_P7.62mm_Horizontal
R3, R4, R5, R6, R7, R8, R9, R10: 1k; R_Axial_DIN0207_L6.3mm_D2.5mm_P7.62mm_Horizontal
RLY1, RLY2, RLY3, RLY4, RLY5, RLY6, RLY7, RLY8, RLY9: SPDTRelay; SMIHRelay
U1: MCP23008; DIP-18_W7.62mm_Socket
U2: ULN2803A; DIP-18_W7.62mm_Socket

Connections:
+5V: C10.2, C11.1, C13.2, J11.9, JP1.3, JP2.3, JP3.3, JP4.3, R1.1, R2.1, U1.6, U1.18
EXTPWR: C33.2, JP4.2, L10.1
GND: C10.1, C11.2, C12.2, C13.1, C15.2, C16.2, C17.2, C18.2, C19.2, C20.2, C21.2, C22.2, C23.1, C33.1, J11.1, J11.4, J11.6, J11.8, J11.10, JP1.1, JP2.1, JP3.1, L9.1, U1.9
unnamed: C12.1, J13.1
unnamed: C14.1, C35.1, J14.1
unnamed: C15.1, L1.1, U1.17
unnamed: C16.1, L2.1, U1.16
unnamed: C17.1, L3.1, U1.15
unnamed: C18.1, L4.1, U1.14
unnamed: C19.1, L5.1, U1.13
unnamed: C20.1, L6.1, U1.12
unnamed: C21.1, L7.1, U1.11
unnamed: C22.1, L8.1, U1.10
unnamed: C23.2, J11.2, J11.5, JP4.1
unnamed: D1.1, R3.1
unnamed: D2.1, R4.1
unnamed: D3.1, R5.1
unnamed: D4.1, R6.1
unnamed: D5.1, R7.1
unnamed: D6.1, R8.1
unnamed: D7.1, R9.1
unnamed: D8.1, R10.1
unnamed: J1.1, LC1.3, RLY1.2
unnamed: J1.2, LC2.4, RLY2.1
unnamed: J2.1, LC2.3, RLY2.2
unnamed: J2.2, LC3.4, RLY3.1
unnamed: J3.1, LC3.3, RLY3.2
unnamed: J3.2, LC4.4, RLY4.1
unnamed: J4.1, LC4.3, RLY4.2
unnamed: J4.2, LC5.4, RLY5.1
unnamed: J5.1, LC5.3, RLY5.2
unnamed: J5.2, LC6.4, RLY6.1
unnamed: J6.1, LC6.3, RLY6.2
unnamed: J6.2, LC7.4, RLY7.1
unnamed: J7.1, LC7.3, RLY7.2
unnamed: J9.1, RLY8.2
unnamed: J10.1, RLY8.3
unnamed: J10.2, J22.1, RLY9.3
unnamed: J12.1, J20.1, J21.1
unnamed: J15.1, J18.1, J19.1
unnamed: J9.2, J16.1, RLY9.2
unnamed: J7.2, J23.1, RLY8.1
unnamed: JP1.2, U1.5
unnamed: JP2.2, U1.4
unnamed: JP3.2, U1.3
unnamed: L1.2, U2.1
unnamed: L2.2, U2.2
unnamed: L3.2, U2.3
unnamed: L4.2, U2.4
unnamed: L5.2, U2.5
unnamed: L6.2, U2.6
unnamed: L7.2, U2.7
unnamed: L8.2, U2.8
unnamed: LC1.1, RLY1.3
unnamed: LC2.1, RLY2.3
unnamed: LC3.1, RLY3.3
unnamed: LC4.1, RLY4.3
unnamed: LC5.1, RLY5.3
unnamed: LC6.1, RLY6.3
unnamed: LC7.1, RLY7.3
RFGND: J8.2, J17.1, J23.2, LC1.2, LC2.2, LC3.2, LC4.2, LC5.2, LC6.2, LC7.2, RLY9.1
RFPORT1: J1.3, J2.3, J3.3, J4.3, J5.3, J6.3, J7.3, J8.1, LC1.4, RLY1.1
RLY1: C1.2, C32.2, R3.2, RLY1.5, U2.11
RLY2: C2.2, C31.2, R4.2, RLY2.5, U2.12
RLY3: C3.2, C30.2, R5.2, RLY3.5, U2.13
RLY4: C4.2, C29.2, R6.2, RLY4.5, U2.14
RLY5: C5.2, C27.2, R7.2, RLY5.5, U2.15
RLY6: C6.2, C26.2, R8.2, RLY6.5, U2.16
RLY7: C7.2, C25.2, R9.2, RLY7.5, U2.17
RLY8: C8.2, C24.2, C28.2, R10.2, RLY8.5, RLY9.5, U2.18
RLYGND: C1.1, C2.1, C3.1, C4.1, C5.1, C6.1, C7.1, C8.1, C9.2, C14.2, C34.2, C35.2, L9.2, P2.1, P3.1, P4.1, P5.1, P6.1, P7.1, P8.1, P9.1, P10.1, P11.1, P12.1, U2.9
RLYPWR: C9.1, C24.1, C25.1, C26.1, C27.1, C28.1, C29.1, C30.1, C31.1, C32.1, C34.1, D1.2, D2.2, D3.2, D4.2, D5.2, D6.2, D7.2, D8.2, L10.2, RLY1.4, RLY2.4, RLY3.4, RLY4.4, RLY5.4, RLY6.4, RLY7.4, RLY8.4, RLY9.4, U2.10
SCL: J11.3, R2.2, U1.1
SDA: J11.7, R1.2, U1.2

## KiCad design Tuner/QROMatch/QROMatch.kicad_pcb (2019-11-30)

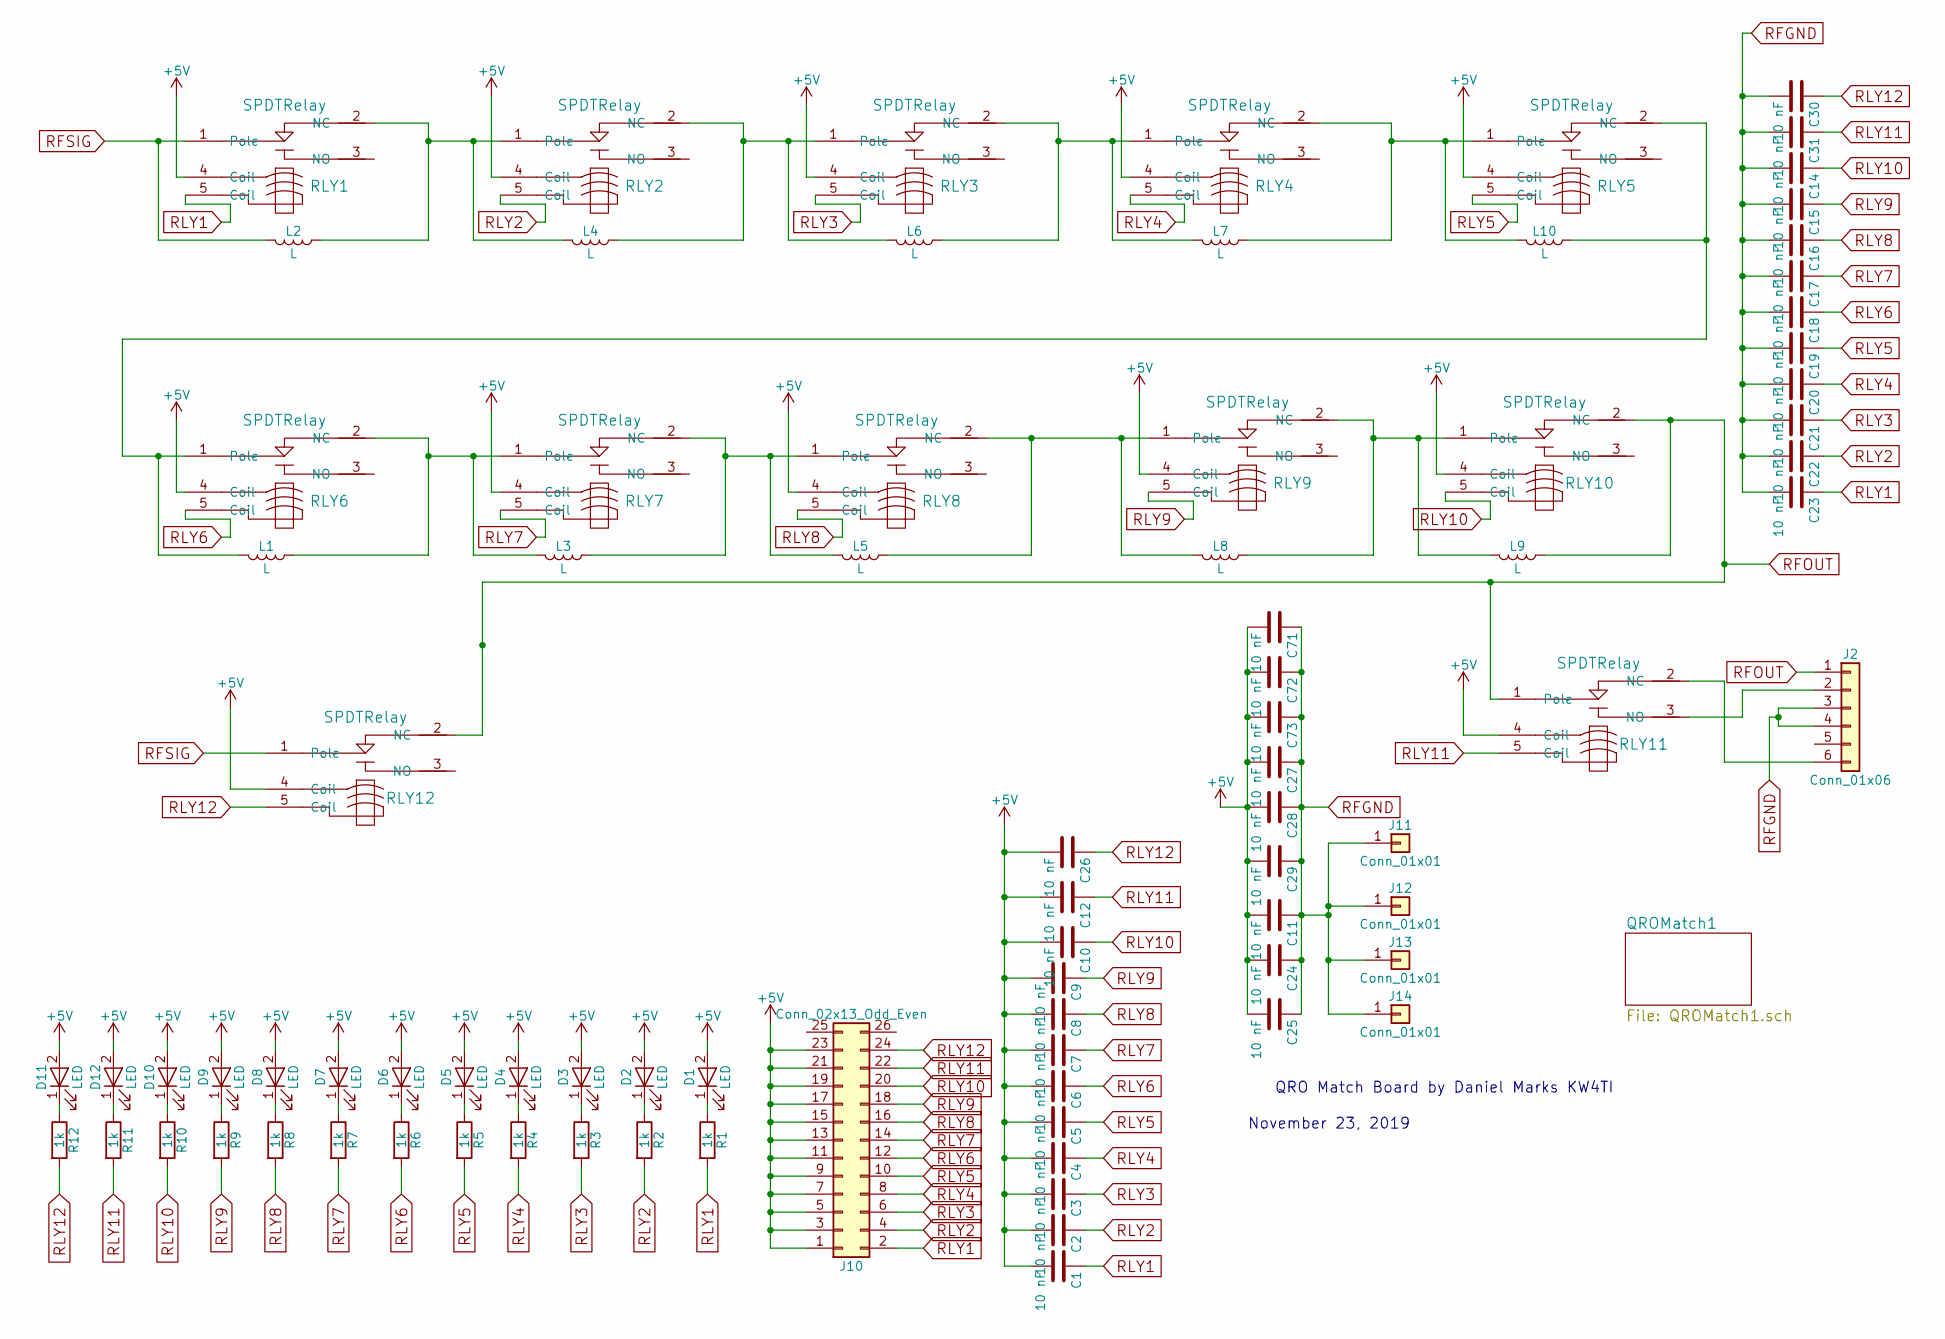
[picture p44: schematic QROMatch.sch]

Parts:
C1, C2, C3, C4, C5, C6, C7, C8, C9, C10, C12, C14, C15, C16, C17, C18, C19, C20, C21, C22, C23, C26, C27, C28, C29, C30, C31, C71, C72, C73: 10 nF; C_Disc_D5.0mm_W2.5mm_P2.50mm
C11, C24, C25: 10 nF; C_Disc_D5.0mm_W2.5mm_P5.00mm
D1, D2, D3, D4, D5, D6, D7, D8, D9, D10, D11, D12: LED; LED_D3.0mm
J2: Conn_01x06; TerminalBlock_bornier-6_P5.08mm
J10: Conn_02x13_Odd_Even; Pin_Header_Straight_2x13_Pitch2.54mm
J11, J12, J13, J14: Conn_01x01; 1pin
L1, L2, L3, L4, L5, L6, L7, L8, L9, L10: L; InductorPad
R1, R2, R3, R4, R5, R6, R7, R8, R9, R10, R11, R12: 1k; R_Axial_DIN0207_L6.3mm_D2.5mm_P7.62mm_Horizontal
RLY1, RLY2, RLY3, RLY4, RLY5, RLY6, RLY7, RLY8, RLY9, RLY10, RLY11, RLY12: SPDTRelay; SMIHRelay

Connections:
+5V: C1.2, C2.2, C3.2, C4.2, C5.2, C6.2, C7.2, C8.2, C9.2, C10.2, C11.2, C12.2, C24.2, C25.2, C26.2, C27.2, C28.2, C29.2, C71.2, C72.2, C73.2, D1.2 (A), D2.2 (A), D3.2 (A), D4.2 (A), D5.2 (A), D6.2 (A), D7.2 (A), D8.2 (A), D9.2 (A), D10.2 (A), D11.2 (A), D12.2 (A), J10.1, J10.3, J10.5, J10.7, J10.9, J10.11, J10.13, J10.15, J10.17, J10.19, J10.21, J10.23, RLY1.4 (Coil), RLY2.4 (Coil), RLY3.4 (Coil), RLY4.4 (Coil), RLY5.4 (Coil), RLY6.4 (Coil), RLY7.4 (Coil), RLY8.4 (Coil), RLY9.4 (Coil), RLY10.4 (Coil), RLY11.4 (Coil), RLY12.4 (Coil)
unnamed: D1.1 (K), R1.1
unnamed: D2.1 (K), R2.1
unnamed: D3.1 (K), R3.1
unnamed: D4.1 (K), R4.1
unnamed: D5.1 (K), R5.1
unnamed: D6.1 (K), R6.1
unnamed: D7.1 (K), R7.1
unnamed: D8.1 (K), R8.1
unnamed: D9.1 (K), R9.1
unnamed: D10.1 (K), R10.1
unnamed: D11.1 (K), R12.1
unnamed: D12.1 (K), R11.1
unnamed: J2.2, RLY11.3 (NO)
unnamed: J2.6, RLY11.2 (NC)
unnamed: L1.1, L3.2, RLY6.2 (NC), RLY7.1 (Pole)
unnamed: L1.2, L10.1, RLY5.2 (NC), RLY6.1 (Pole)
unnamed: L2.1, L4.2, RLY1.2 (NC), RLY2.1 (Pole)
unnamed: L3.1, L5.2, RLY7.2 (NC), RLY8.1 (Pole)
unnamed: L4.1, L6.2, RLY2.2 (NC), RLY3.1 (Pole)
unnamed: L5.1, L8.2, RLY8.2 (NC), RLY9.1 (Pole)
unnamed: L6.1, L7.2, RLY3.2 (NC), RLY4.1 (Pole)
unnamed: L8.1, L9.2, RLY9.2 (NC), RLY10.1 (Pole)
unnamed: L7.1, L10.2, RLY4.2 (NC), RLY5.1 (Pole)
RFGND: C11.1, C14.2, C15.2, C16.2, C17.2, C18.2, C19.2, C20.2, C21.2, C22.2, C23.2, C24.1, C25.1, C27.1, C28.1, C29.1, C30.2, C31.2, C71.1, C72.1, C73.1, J2.3, J2.4, J11.1, J12.1, J13.1, J14.1; also elsewhere on the board
RFOUT: J2.1, L9.1, RLY10.2 (NC), RLY11.1 (Pole), RLY12.2 (NC); also elsewhere on the board
RFSIG: L2.2, RLY1.1 (Pole), RLY12.1 (Pole); also elsewhere on the board
RLY1: C1.1, C23.1, J10.2, R1.2, RLY1.5 (Coil)
RLY2: C2.1, C22.1, J10.4, R2.2, RLY2.5 (Coil)
RLY3: C3.1, C21.1, J10.6, R3.2, RLY3.5 (Coil)
RLY4: C4.1, C20.1, J10.8, R4.2, RLY4.5 (Coil)
RLY5: C5.1, C19.1, J10.10, R5.2, RLY5.5 (Coil)
RLY6: C6.1, C18.1, J10.12, R6.2, RLY6.5 (Coil)
RLY7: C7.1, C17.1, J10.14, R7.2, RLY7.5 (Coil)
RLY8: C8.1, C16.1, J10.16, R8.2, RLY8.5 (Coil)
RLY9: C9.1, C15.1, J10.18, R9.2, RLY9.5 (Coil)
RLY10: C10.1, C14.1, J10.20, R10.2, RLY10.5 (Coil)
RLY11: C12.1, C31.1, J10.22, R11.2, RLY11.5 (Coil)
RLY12: C26.1, C30.1, J10.24, R12.2, RLY12.5 (Coil)

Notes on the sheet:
QRO Match Board by Daniel Marks KW4TI
November 23, 2019

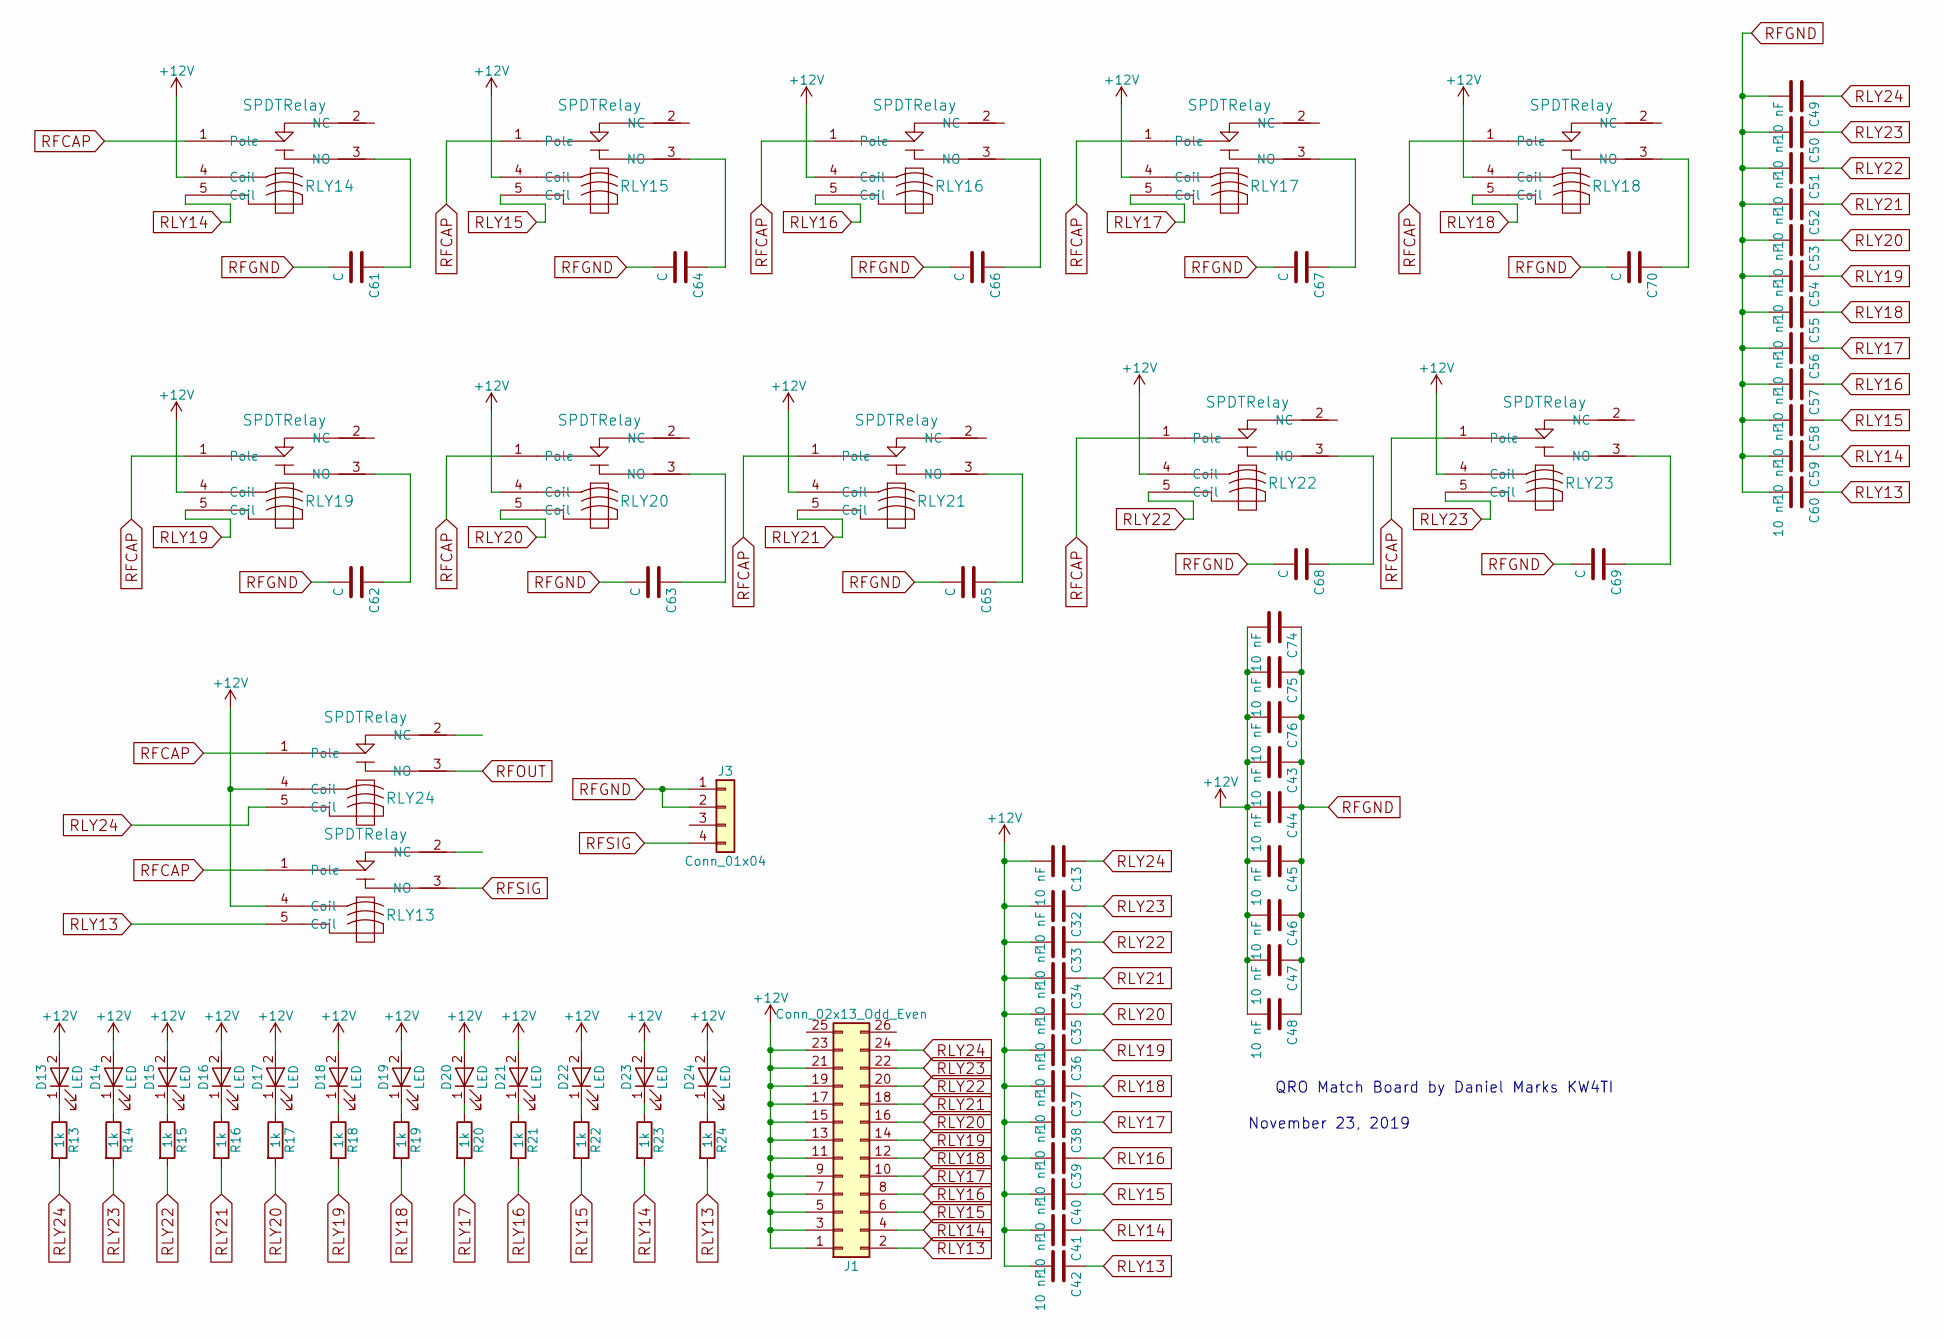
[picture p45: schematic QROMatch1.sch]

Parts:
C13, C32, C33, C34, C35, C36, C37, C38, C39, C40, C41, C42, C43, C44, C45, C49, C50, C51, C52, C53, C54, C55, C56, C57, C58, C59, C60, C74, C75, C76: 10 nF; C_Disc_D5.0mm_W2.5mm_P2.50mm
C46, C47, C48: 10 nF; C_Disc_D5.0mm_W2.5mm_P5.00mm
C61, C62, C63, C64, C65, C66, C67, C68, C69, C70: C; CapacitorPad
D13, D14, D15, D16, D17, D18, D19, D20, D21, D22, D23, D24: LED; LED_D3.0mm
J1: Conn_02x13_Odd_Even; Pin_Header_Straight_2x13_Pitch2.54mm
J3: Conn_01x04; TerminalBlock_bornier-4_P5.08mm
R13, R14, R15, R16, R17, R18, R19, R20, R21, R22, R23, R24: 1k; R_Axial_DIN0207_L6.3mm_D2.5mm_P7.62mm_Horizontal
RLY13, RLY14, RLY15, RLY16, RLY17, RLY18, RLY19, RLY20, RLY21, RLY22, RLY23, RLY24: SPDTRelay; SMIHRelay

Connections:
+12V: C13.2, C32.2, C33.2, C34.2, C35.2, C36.2, C37.2, C38.2, C39.2, C40.2, C41.2, C42.2, C43.2, C44.2, C45.2, C46.2, C47.2, C48.2, C74.2, C75.2, C76.2, D13.2 (A), D14.2 (A), D15.2 (A), D16.2 (A), D17.2 (A), D18.2 (A), D19.2 (A), D20.2 (A), D21.2 (A), D22.2 (A), D23.2 (A), D24.2 (A), J1.1, J1.3, J1.5, J1.7, J1.9, J1.11, J1.13, J1.15, J1.17, J1.19, J1.21, J1.23, RLY13.4 (Coil), RLY14.4 (Coil), RLY15.4 (Coil), RLY16.4 (Coil), RLY17.4 (Coil), RLY18.4 (Coil), RLY19.4 (Coil), RLY20.4 (Coil), RLY21.4 (Coil), RLY22.4 (Coil), RLY23.4 (Coil), RLY24.4 (Coil)
unnamed: C61.1, RLY14.3 (NO)
unnamed: C62.1, RLY19.3 (NO)
unnamed: C63.1, RLY20.3 (NO)
unnamed: C64.1, RLY15.3 (NO)
unnamed: C65.1, RLY21.3 (NO)
unnamed: C66.1, RLY16.3 (NO)
unnamed: C67.1, RLY17.3 (NO)
unnamed: C68.1, RLY22.3 (NO)
unnamed: C69.1, RLY23.3 (NO)
unnamed: C70.1, RLY18.3 (NO)
unnamed: D13.1 (K), R13.1
unnamed: D14.1 (K), R14.1
unnamed: D15.1 (K), R15.1
unnamed: D16.1 (K), R16.1
unnamed: D17.1 (K), R17.1
unnamed: D18.1 (K), R18.1
unnamed: D19.1 (K), R19.1
unnamed: D20.1 (K), R20.1
unnamed: D21.1 (K), R21.1
unnamed: D22.1 (K), R22.1
unnamed: D23.1 (K), R23.1
unnamed: D24.1 (K), R24.1
RFCAP: RLY13.1 (Pole), RLY14.1 (Pole), RLY15.1 (Pole), RLY16.1 (Pole), RLY17.1 (Pole), RLY18.1 (Pole), RLY19.1 (Pole), RLY20.1 (Pole), RLY21.1 (Pole), RLY22.1 (Pole), RLY23.1 (Pole), RLY24.1 (Pole)
RFGND: C43.1, C44.1, C45.1, C46.1, C47.1, C48.1, C49.2, C50.2, C51.2, C52.2, C53.2, C54.2, C55.2, C56.2, C57.2, C58.2, C59.2, C60.2, C61.2, C62.2, C63.2, C64.2, C65.2, C66.2, C67.2, C68.2, C69.2, C70.2, C74.1, C75.1, C76.1, J3.1, J3.2; also elsewhere on the board
RFOUT: RLY24.3 (NO); also elsewhere on the board
RFSIG: J3.4, RLY13.3 (NO); also elsewhere on the board
RLY13: C42.1, C60.1, J1.2, R24.2, RLY13.5 (Coil)
RLY14: C41.1, C59.1, J1.4, R23.2, RLY14.5 (Coil)
RLY15: C40.1, C58.1, J1.6, R22.2, RLY15.5 (Coil)
RLY16: C39.1, C57.1, J1.8, R21.2, RLY16.5 (Coil)
RLY17: C38.1, C56.1, J1.10, R20.2, RLY17.5 (Coil)
RLY18: C37.1, C55.1, J1.12, R19.2, RLY18.5 (Coil)
RLY19: C36.1, C54.1, J1.14, R18.2, RLY19.5 (Coil)
RLY20: C35.1, C53.1, J1.16, R17.2, RLY20.5 (Coil)
RLY21: C34.1, C52.1, J1.18, R16.2, RLY21.5 (Coil)
RLY22: C33.1, C51.1, J1.20, R15.2, RLY22.5 (Coil)
RLY23: C32.1, C50.1, J1.22, R14.2, RLY23.5 (Coil)
RLY24: C13.1, C49.1, J1.24, R13.2, RLY24.5 (Coil)

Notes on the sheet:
QRO Match Board by Daniel Marks KW4TI
November 23, 2019

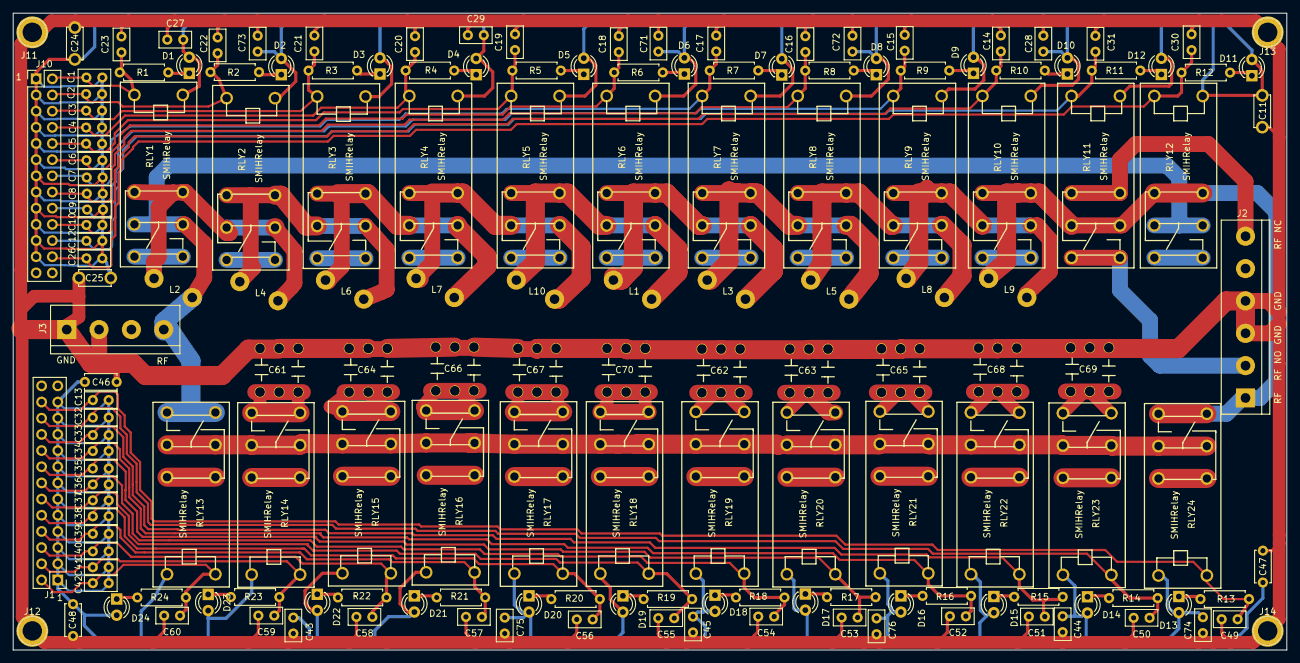
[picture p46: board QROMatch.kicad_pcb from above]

Board: 2 copper layers, 200.0 x 100.0 mm, 166 parts (0 on the bottom side), 75 nets.

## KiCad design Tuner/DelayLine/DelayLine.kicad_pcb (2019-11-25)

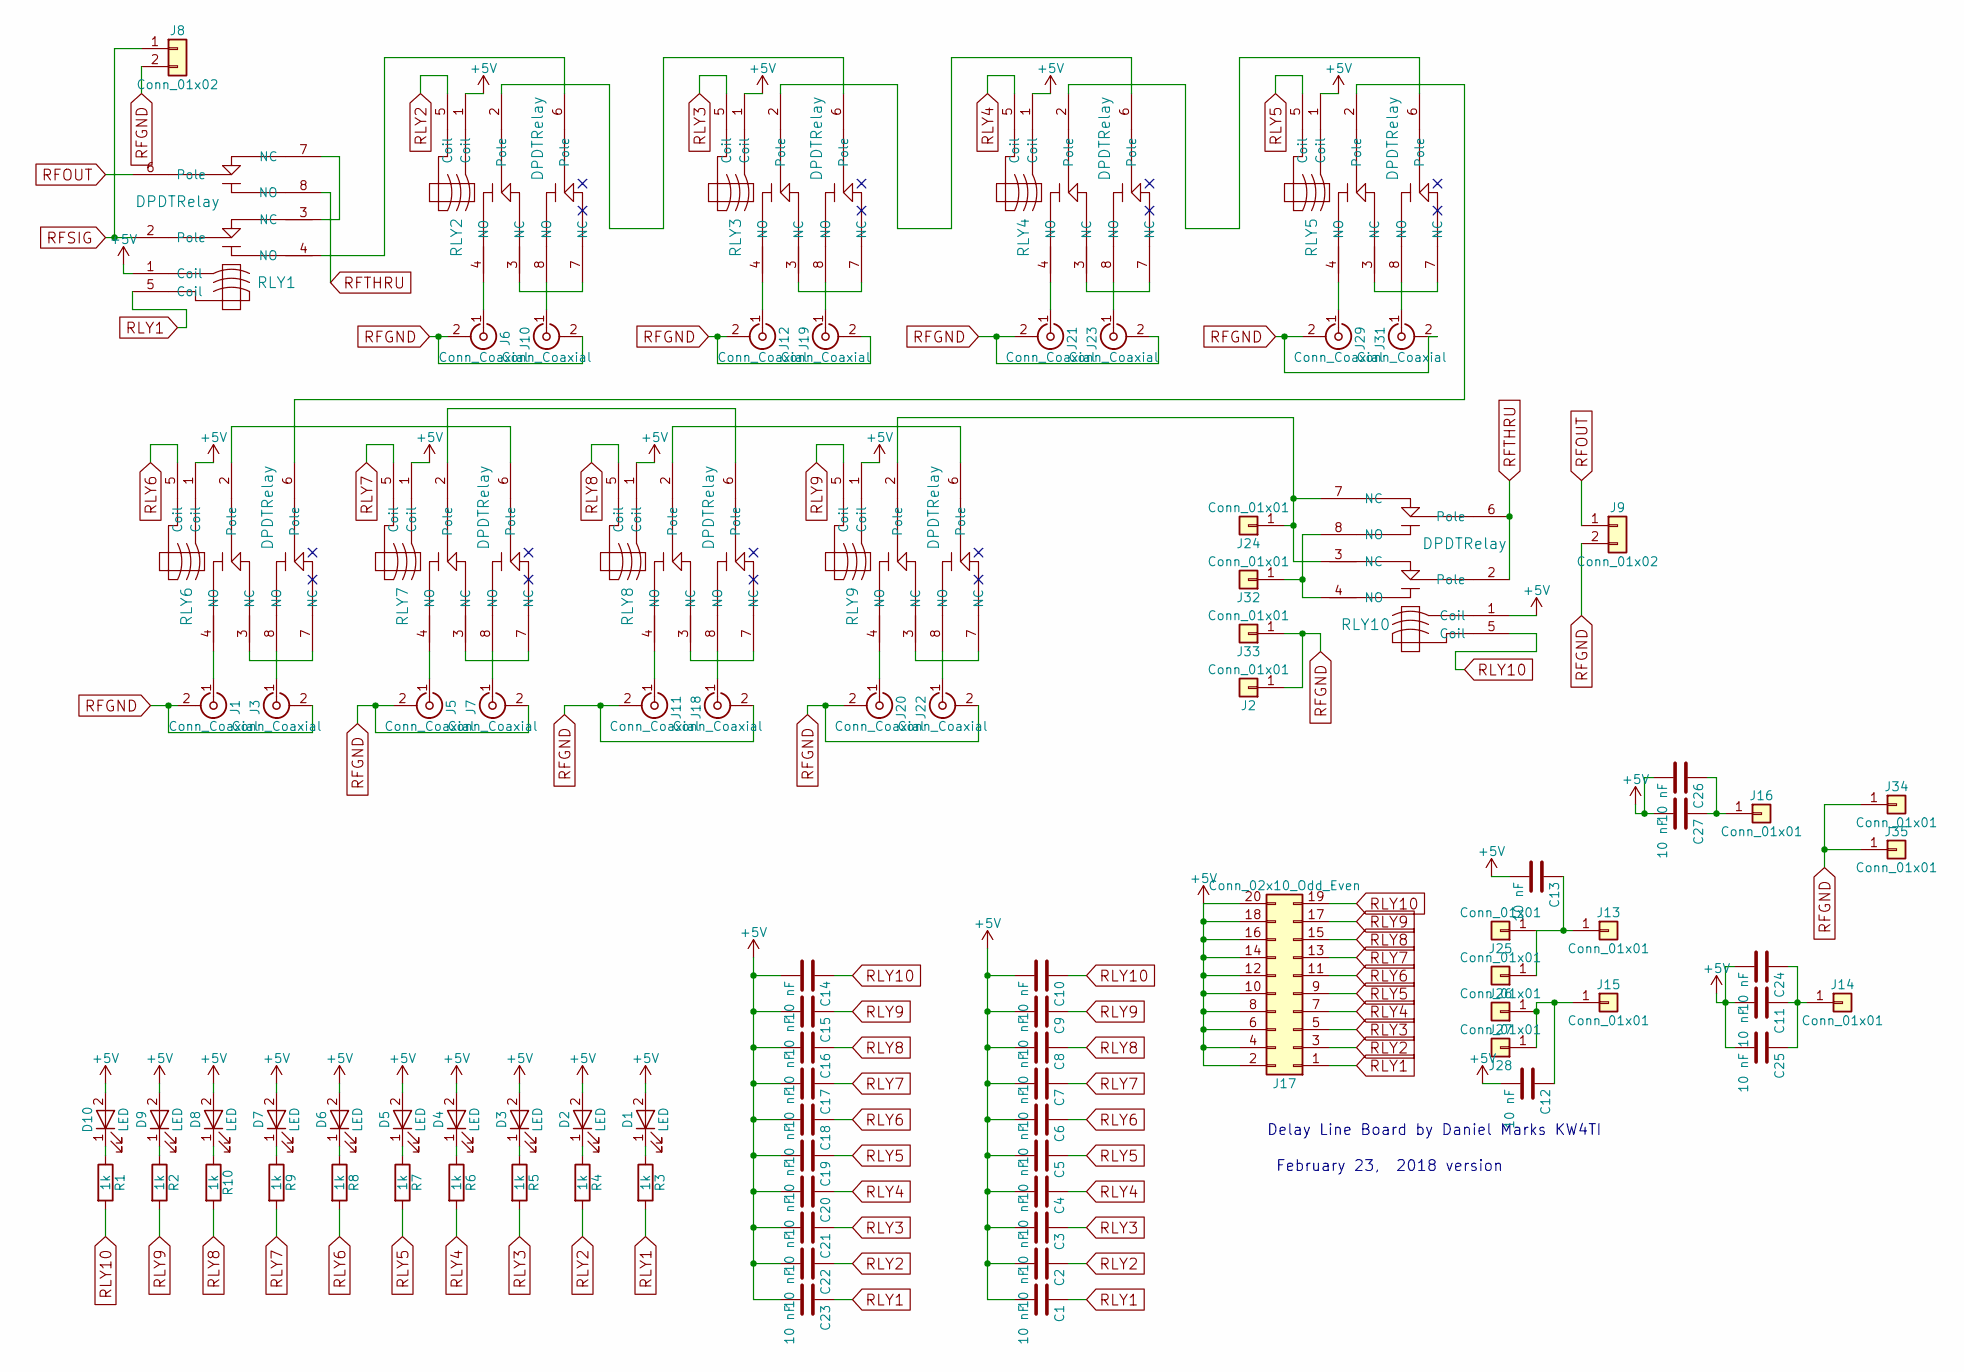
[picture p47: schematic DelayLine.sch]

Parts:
C1, C2, C3, C4, C5, C6, C7, C8, C9, C10, C12, C13, C14, C15, C16, C17, C18, C19, C20, C21, C22, C23: 10 nF; C_Disc_D5.0mm_W2.5mm_P2.50mm
C11, C24, C25, C26, C27: 10 nF; C_Disc_D5.0mm_W2.5mm_P5.00mm
D1, D2, D3, D4, D5, D6, D7, D8, D9, D10: LED; LED_D3.0mm
J1, J3, J5, J6, J7, J10, J11, J12, J18, J19, J20, J21, J22, J23, J29, J31: Conn_Coaxial; bnc-ci
J2, J13, J14, J15, J16, J24, J32, J33: Conn_01x01; 1pin
J8, J9: Conn_01x02; bnc_90_1-1337543-0_pad_combo
J17: Conn_02x10_Odd_Even; Pin_Header_Straight_2x10_Pitch2.54mm
J25, J26, J27, J28, J34, J35: Conn_01x01; SOLDERJUMPER
R1, R2, R3, R4, R5, R6, R7, R8, R9, R10: 1k; R_Axial_DIN0207_L6.3mm_D2.5mm_P7.62mm_Horizontal
RLY1, RLY2, RLY3, RLY4, RLY5, RLY6, RLY7, RLY8, RLY9, RLY10: DPDTRelay; G2VRelay

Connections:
+5V: C1.2, C2.2, C3.2, C4.2, C5.2, C6.2, C7.2, C8.2, C9.2, C10.2, C11.2, C12.2, C13.2, C14.2, C15.2, C16.2, C17.2, C18.2, C19.2, C20.2, C21.2, C22.2, C23.2, C24.2, C25.2, C26.2, C27.2, D1.2 (A), D2.2 (A), D3.2 (A), D4.2 (A), D5.2 (A), D6.2 (A), D7.2 (A), D8.2 (A), D9.2 (A), D10.2 (A), J17.2, J17.4, J17.6, J17.8, J17.10, J17.12, J17.14, J17.16, J17.18, J17.20, RLY1.1 (Coil), RLY2.1 (Coil), RLY3.1 (Coil), RLY4.1 (Coil), RLY5.1 (Coil), RLY6.1 (Coil), RLY7.1 (Coil), RLY8.1 (Coil), RLY9.1 (Coil), RLY10.1 (Coil)
unnamed: C11.1, C24.1, C25.1, J14.1
unnamed: C12.1, J15.1, J27.1, J28.1
unnamed: C13.1, J13.1, J25.1, J26.1
unnamed: C26.1, C27.1, J16.1
unnamed: D1.1 (K), R3.1
unnamed: D2.1 (K), R4.1
unnamed: D3.1 (K), R5.1
unnamed: D4.1 (K), R6.1
unnamed: D5.1 (K), R7.1
unnamed: D6.1 (K), R8.1
unnamed: D7.1 (K), R9.1
unnamed: D8.1 (K), R10.1
unnamed: D9.1 (K), R2.1
unnamed: D10.1 (K), R1.1
unnamed: J1.1 (In), RLY6.4 (NO)
unnamed: J3.1 (In), RLY6.8 (NO)
unnamed: J5.1 (In), RLY7.4 (NO)
unnamed: J6.1 (In), RLY2.4 (NO)
unnamed: J7.1 (In), RLY7.8 (NO)
unnamed: J10.1 (In), RLY2.8 (NO)
unnamed: J11.1 (In), RLY8.4 (NO)
unnamed: J12.1 (In), RLY3.4 (NO)
unnamed: J18.1 (In), RLY8.8 (NO)
unnamed: J19.1 (In), RLY3.8 (NO)
unnamed: J20.1 (In), RLY9.4 (NO)
unnamed: J21.1 (In), RLY4.4 (NO)
unnamed: J22.1 (In), RLY9.8 (NO)
unnamed: J23.1 (In), RLY4.8 (NO)
unnamed: J24.1, RLY9.2 (Pole), RLY10.3 (NC), RLY10.7 (NC)
unnamed: J29.1 (In), RLY5.4 (NO)
unnamed: J31.1 (In), RLY5.8 (NO)
unnamed: J32.1, RLY10.4 (NO), RLY10.8 (NO)
unnamed: RLY1.3 (NC), RLY1.7 (NC)
unnamed: RLY1.4 (NO), RLY2.6 (Pole)
unnamed: RLY2.2 (Pole), RLY3.6 (Pole)
unnamed: RLY2.3 (NC), RLY2.7 (NC)
unnamed: RLY3.2 (Pole), RLY4.6 (Pole)
unnamed: RLY3.3 (NC), RLY3.7 (NC)
unnamed: RLY4.2 (Pole), RLY5.6 (Pole)
unnamed: RLY4.3 (NC), RLY4.7 (NC)
unnamed: RLY5.2 (Pole), RLY6.6 (Pole)
unnamed: RLY5.3 (NC), RLY5.7 (NC)
unnamed: RLY6.2 (Pole), RLY7.6 (Pole)
unnamed: RLY6.3 (NC), RLY6.7 (NC)
unnamed: RLY7.2 (Pole), RLY8.6 (Pole)
unnamed: RLY7.3 (NC), RLY7.7 (NC)
unnamed: RLY8.2 (Pole), RLY9.6 (Pole)
unnamed: RLY8.3 (NC), RLY8.7 (NC)
unnamed: RLY9.3 (NC), RLY9.7 (NC)
RFGND: J1.2 (Ext), J2.1, J3.2 (Ext), J5.2 (Ext), J6.2 (Ext), J7.2 (Ext), J8.2, J9.2, J10.2 (Ext), J11.2 (Ext), J12.2 (Ext), J18.2 (Ext), J19.2 (Ext), J20.2 (Ext), J21.2 (Ext), J22.2 (Ext), J23.2 (Ext), J29.2 (Ext), J31.2 (Ext), J33.1, J34.1, J35.1
RFOUT: J9.1, RLY1.6 (Pole)
RFSIG: J8.1, RLY1.2 (Pole)
RFTHRU: RLY1.8 (NO), RLY10.2 (Pole), RLY10.6 (Pole)
RLY1: C1.1, C23.1, J17.1, R3.2, RLY1.5 (Coil)
RLY2: C2.1, C22.1, J17.3, R4.2, RLY2.5 (Coil)
RLY3: C3.1, C21.1, J17.5, R5.2, RLY3.5 (Coil)
RLY4: C4.1, C20.1, J17.7, R6.2, RLY4.5 (Coil)
RLY5: C5.1, C19.1, J17.9, R7.2, RLY5.5 (Coil)
RLY6: C6.1, C18.1, J17.11, R8.2, RLY6.5 (Coil)
RLY7: C7.1, C17.1, J17.13, R9.2, RLY7.5 (Coil)
RLY8: C8.1, C16.1, J17.15, R10.2, RLY8.5 (Coil)
RLY9: C9.1, C15.1, J17.17, R2.2, RLY9.5 (Coil)
RLY10: C10.1, C14.1, J17.19, R1.2, RLY10.5 (Coil)

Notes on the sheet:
Delay Line Board by Daniel Marks KW4TI
February 23, 2018 version

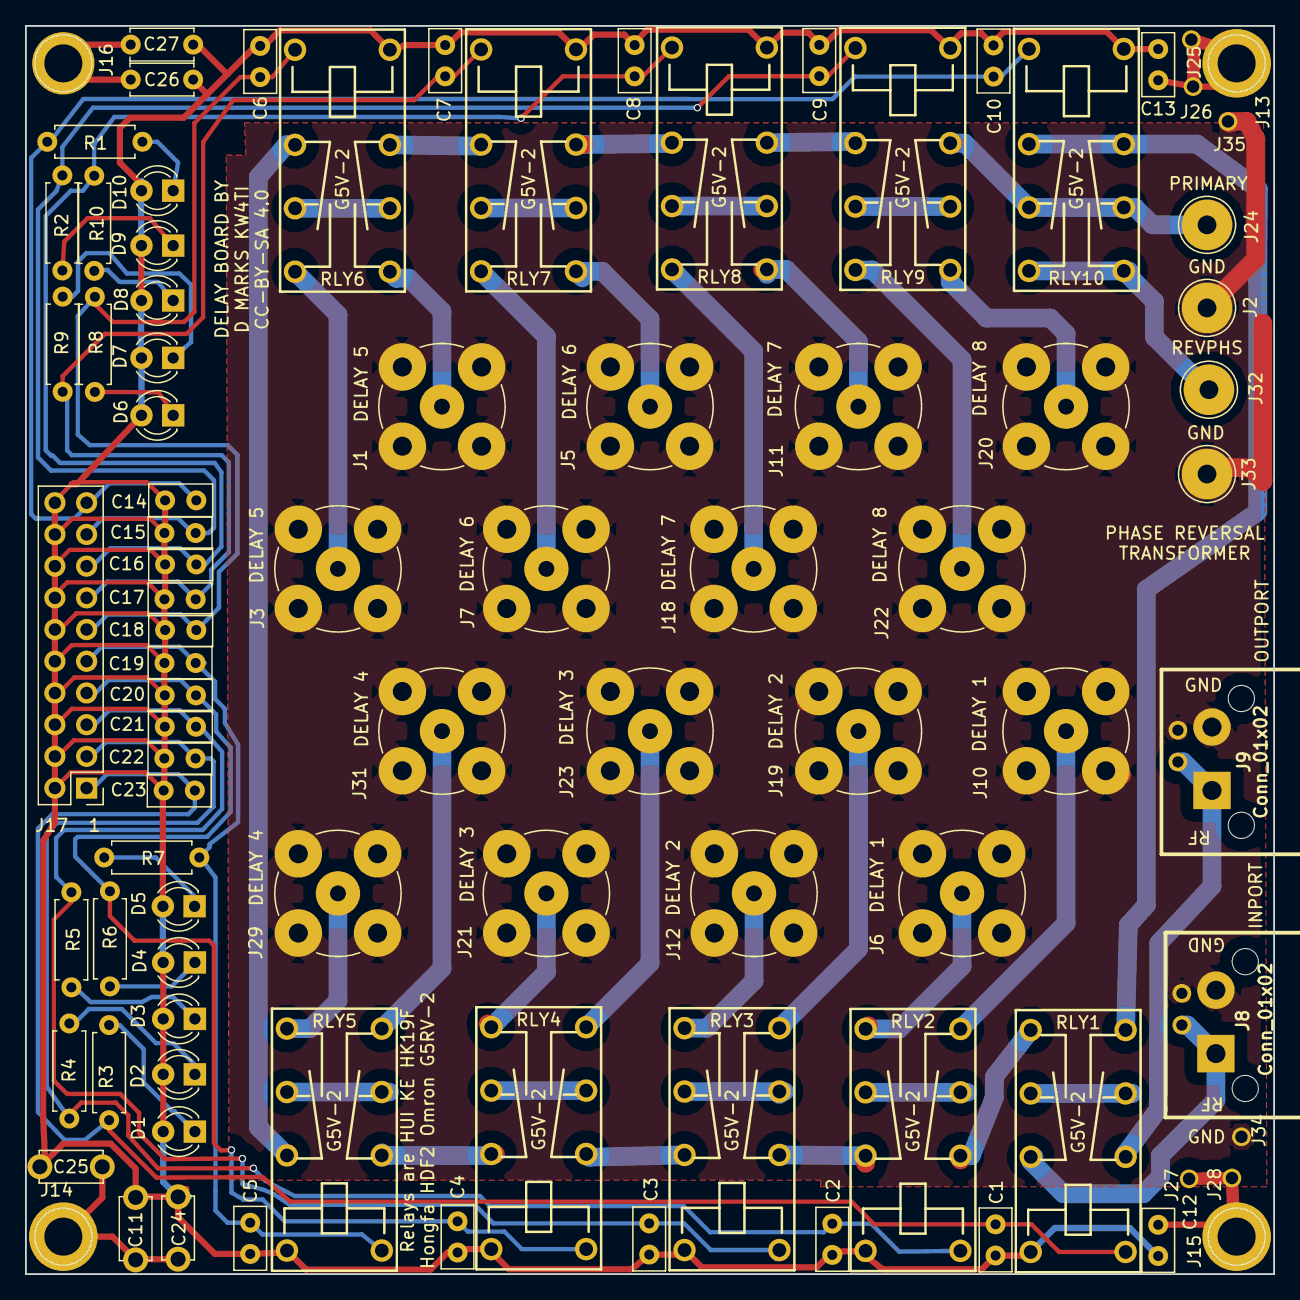
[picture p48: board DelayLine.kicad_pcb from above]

Board: 2 copper layers, 100.0 x 100.0 mm, 90 parts (0 on the bottom side), 64 nets.

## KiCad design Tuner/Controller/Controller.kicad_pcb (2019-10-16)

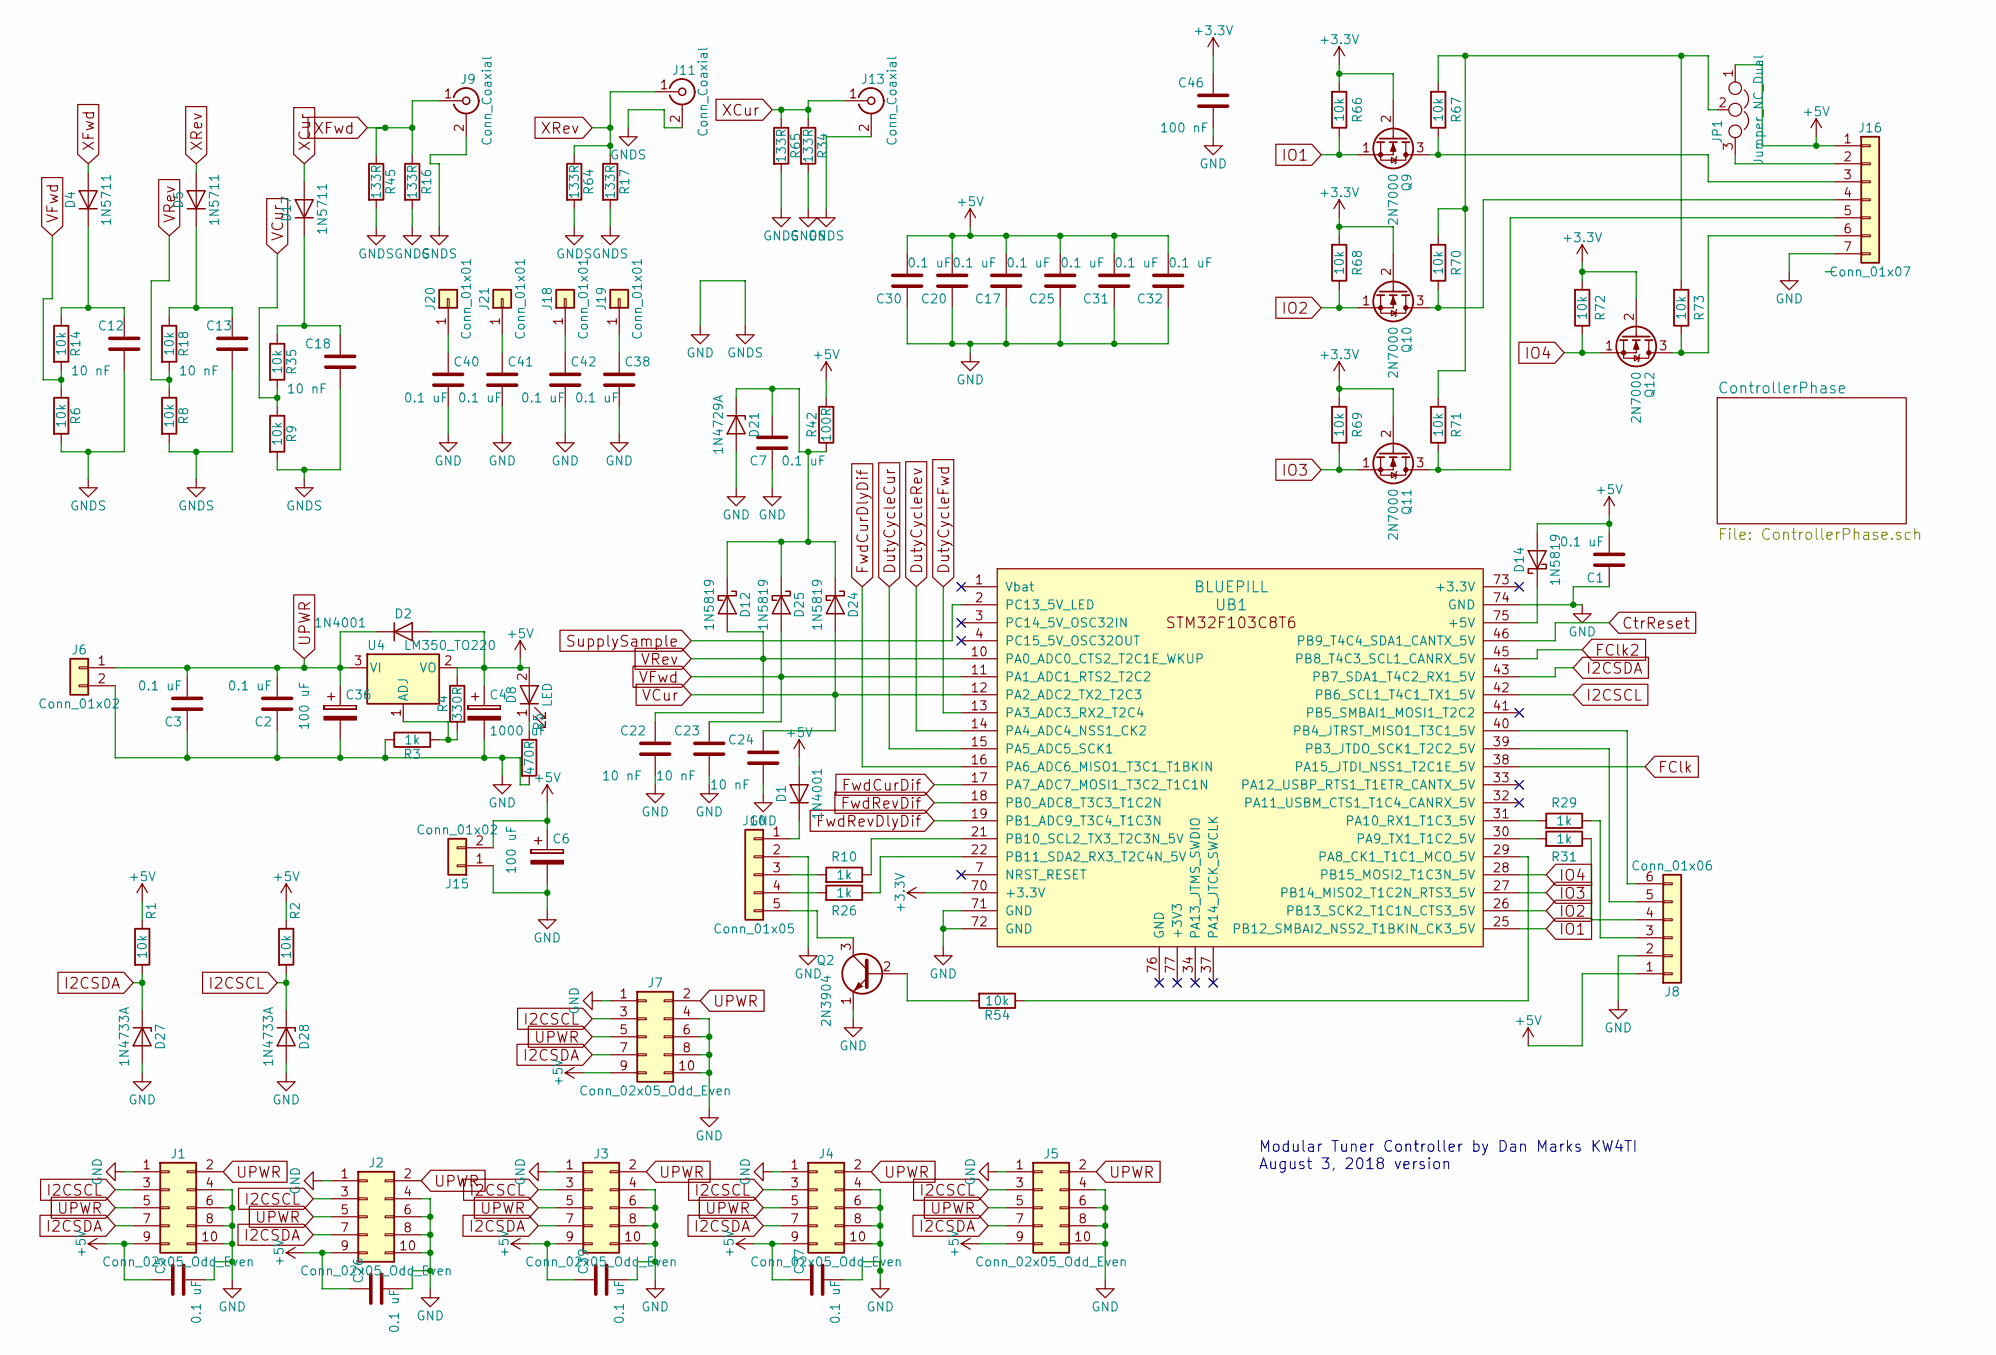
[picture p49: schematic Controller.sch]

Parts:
C1, C2, C7: 0.1 uF; C_Disc_D5.0mm_W2.5mm_P5.00mm
C3, C5, C17, C20, C25, C26, C30, C31, C32, C37, C38, C39, C40, C41, C42: 0.1 uF; C_Disc_D5.0mm_W2.5mm_P2.50mm
C4: 1000 uF; CP_Radial_D10.0mm_P5.00mm
C6, C36: 100 uF; CP_Radial_D5.0mm_P2.50mm
C12, C13, C18: 10 nF; C_Disc_D5.0mm_W2.5mm_P2.50mm
C22, C23, C24: 10 nF; C_Disc_D5.0mm_W2.5mm_P5.00mm
C46: 100 nF; C_Disc_D5.0mm_W2.5mm_P2.50mm
D1, D2: 1N4001; D_DO-41_SOD81_P7.62mm_Horizontal
D4, D5, D17: 1N5711; D_DO-35_SOD27_P7.62mm_Horizontal
D8: LED; LED_D3.0mm
D12, D14, D24, D25: 1N5819; D_DO-41_SOD81_P7.62mm_Horizontal
D21: 1N4729A; D_DO-41_SOD81_P7.62mm_Horizontal
D27, D28: 1N4733A; D_DO-41_SOD81_P7.62mm_Horizontal
J1, J2, J3, J4, J5, J7: Conn_02x05_Odd_Even; Pin_Header_Straight_2x05_Pitch2.54mm
J6, J15: Conn_01x02; TerminalBlock_bornier-2_P5.08mm
J8: Conn_01x06; Pin_Header_Straight_1x06_Pitch2.54mm
J9, J11, J13: Conn_Coaxial; bnc_90_1-1337543-0_pad_combo
J10: Conn_01x05; Pin_Header_Straight_1x05_Pitch2.54mm
J16: Conn_01x07; Pin_Header_Straight_1x07_Pitch2.54mm
J18, J19, J20, J21: Conn_01x01; 1pin
JP1: Jumper_NC_Dual; Pin_Header_Straight_1x03_Pitch2.54mm
Q2: 2N3904; TO-92_Molded_Narrow
Q9, Q10, Q11, Q12: 2N7000; TO-92_Molded_Narrow
R1, R2, R6, R8, R9, R14, R18, R35, R54, R66, R67, R68, R69, R70, R71, R72, R73: 10k; R_Axial_DIN0207_L6.3mm_D2.5mm_P7.62mm_Horizontal
R3, R10, R26, R29, R31: 1k; R_Axial_DIN0207_L6.3mm_D2.5mm_P7.62mm_Horizontal
R4: 330R; R_Axial_DIN0207_L6.3mm_D2.5mm_P7.62mm_Horizontal
R5: 470R; R_Axial_DIN0207_L6.3mm_D2.5mm_P7.62mm_Horizontal
R16, R17, R34, R45, R64, R65: 133R; R_Axial_DIN0309_L9.0mm_D3.2mm_P12.70mm_Horizontal
R42: 100R; R_Axial_DIN0207_L6.3mm_D2.5mm_P7.62mm_Horizontal
U4: LM350_TO220; TO-220-3_Vertical
UB1: BLUEPILL

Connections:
+3V3: C46.1, Q9.2 (G), Q10.2 (G), Q11.2 (G), Q12.2 (G), R66.2, R68.2, R69.2, R72.2, UB1.70 (+3.3V)
CtrReset: UB1.46 (PB9_T4C4_SDA1_CANTX_5V); also elsewhere on the board
DutyCycleCur: UB1.15 (PA5_ADC5_SCK1); also elsewhere on the board
DutyCycleFwd: UB1.13 (PA3_ADC3_RX2_T2C4); also elsewhere on the board
DutyCycleRev: UB1.14 (PA4_ADC4_NSS1_CK2); also elsewhere on the board
FClk2: UB1.45 (PB8_T4C3_SCL1_CANRX_5V); also elsewhere on the board
FwdCurDif: UB1.17 (PA7_ADC7_MOSI1_T3C2_T1C1N); also elsewhere on the board
FwdCurDlyDif: UB1.16 (PA6_ADC6_MISO1_T3C1_T1BKIN); also elsewhere on the board
FwdRevDif: UB1.18 (PB0_ADC8_T3C3_T1C2N); also elsewhere on the board
FwdRevDlyDif: UB1.19 (PB1_ADC9_T3C4_T1C3N); also elsewhere on the board
GND: C1.1, C2.1, C3.1, C4.2, C5.2, C6.2, C7.1, C12.2, C13.2, C17.1, C18.2, C20.1, C22.2, C23.2, C24.2, C25.1, C26.2, C30.1, C31.1, C32.1, C36.2, C37.2, C38.2, C39.2, C40.2, C41.2, C42.2, C46.2, D21.2 (A), D27.2 (A), D28.2 (A), J1.1, J1.4, J1.6, J1.8, J1.10, J2.1, J2.4, J2.6, J2.8, J2.10, J3.1, J3.4, J3.6, J3.8, J3.10, J4.1, J4.4, J4.6, J4.8, J4.10, J5.1, J5.4, J5.6, J5.8, J5.10, J6.2, J7.1, J7.4, J7.6, J7.8, J7.10, J8.2, J9.2 (Ext), J10.2, J11.2 (Ext), J13.2 (Ext), J15.1, J16.7, Q2.1 (E), R3.1, R5.2, R6.2, R8.2, R9.2, R16.2, R17.2, R34.2, R45.2, R64.2, R65.2, UB1.71 (GND), UB1.72 (GND), UB1.74 (GND); also elsewhere on the board
I2CSCL: D28.1 (K), J1.3, J2.3, J3.3, J4.3, J5.3, J7.3, R2.2, UB1.42 (PB6_SCL1_T4C1_TX1_5V)
I2CSDA: D27.1 (K), J1.7, J2.7, J3.7, J4.7, J5.7, J7.7, R1.2, UB1.43 (PB7_SDA1_T4C2_RX1_5V)
IO1: Q9.1 (S), R66.1, UB1.25 (PB12_SMBAI2_NSS2_T1BKIN_CK3_5V)
IO2: Q10.1 (S), R68.1, UB1.26 (PB13_SCK2_T1C1N_CTS3_5V)
IO3: Q11.1 (S), R69.1, UB1.27 (PB14_MISO2_T1C2N_RTS3_5V)
IO4: Q12.1 (S), R72.1, UB1.28 (PB15_MOSI2_T1C3N_5V)
unnamed: C7.2, D12.1 (K), D21.1 (K), D24.1 (K), D25.1 (K), R42.1
unnamed: C12.1, D4.1 (K), R14.1
unnamed: C13.1, D5.1 (K), R18.1
unnamed: C18.1, D17.1 (K), R35.1
unnamed: C38.1, J19.1
unnamed: C40.1, J20.1
unnamed: C41.1, J21.1
unnamed: C42.1, J18.1
unnamed: D1.1 (K), J10.1
unnamed: D8.1 (K), R5.1
unnamed: D14.1 (K), UB1.75 (+5V)
unnamed: J8.3, R29.1
unnamed: J8.4, R31.1
unnamed: J8.5, UB1.39 (PB3_JTDO_SCK1_T2C2_5V)
unnamed: J8.6, UB1.40 (PB4_JTRST_MISO1_T3C1_5V)
unnamed: J10.3, R10.2
unnamed: J10.4, R26.2
unnamed: J10.5, Q2.3 (C)
unnamed: J16.2, JP1.3
unnamed: J16.3, Q9.3 (D), R67.1
unnamed: J16.4, Q10.3 (D), R70.1
unnamed: J16.5, Q11.3 (D), R71.1
unnamed: J16.6, Q12.3 (D), R73.1
unnamed: JP1.2, R67.2, R70.2, R71.2, R73.2
unnamed: Q2.2 (B), R54.2
unnamed: R3.2, R4.2, U4.1 (ADJ)
unnamed: R10.1, UB1.21 (PB10_SCL2_TX3_T2C3N_5V)
unnamed: R26.1, UB1.22 (PB11_SDA2_RX3_T2C4N_5V)
unnamed: R29.2, UB1.31 (PA10_RX1_T1C3_5V)
unnamed: R31.2, UB1.30 (PA9_TX1_T1C2_5V)
unnamed: R54.1, UB1.29 (PA8_CK1_T1C1_MCO_5V)
SupplySample: UB1.2 (PC13_5V_LED); also elsewhere on the board
UPWR: C2.2, C3.2, C36.1, D2.1 (K), J1.2, J1.5, J2.2, J2.5, J3.2, J3.5, J4.2, J4.5, J5.2, J5.5, J6.1, J7.2, J7.5, U4.3 (VI)
VCur: C24.1, D24.2 (A), R9.1, R35.2, UB1.12 (PA2_ADC2_TX2_T2C3)
VFwd: C23.1, D25.2 (A), R6.1, R14.2, UB1.11 (PA1_ADC1_RTS2_T2C2)
VRev: C22.1, D12.2 (A), R8.1, R18.2, UB1.10 (PA0_ADC0_CTS2_T2C1E_WKUP)
XCur: D17.2 (A), J13.1 (In), R34.1, R65.1; also elsewhere on the board
XFwd: D4.2 (A), J9.1 (In), R16.1, R45.1; also elsewhere on the board
XRev: D5.2 (A), J11.1 (In), R17.1, R64.1; also elsewhere on the board

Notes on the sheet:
Modular Tuner Controller by Dan Marks KW4TI August 3, 2018 version

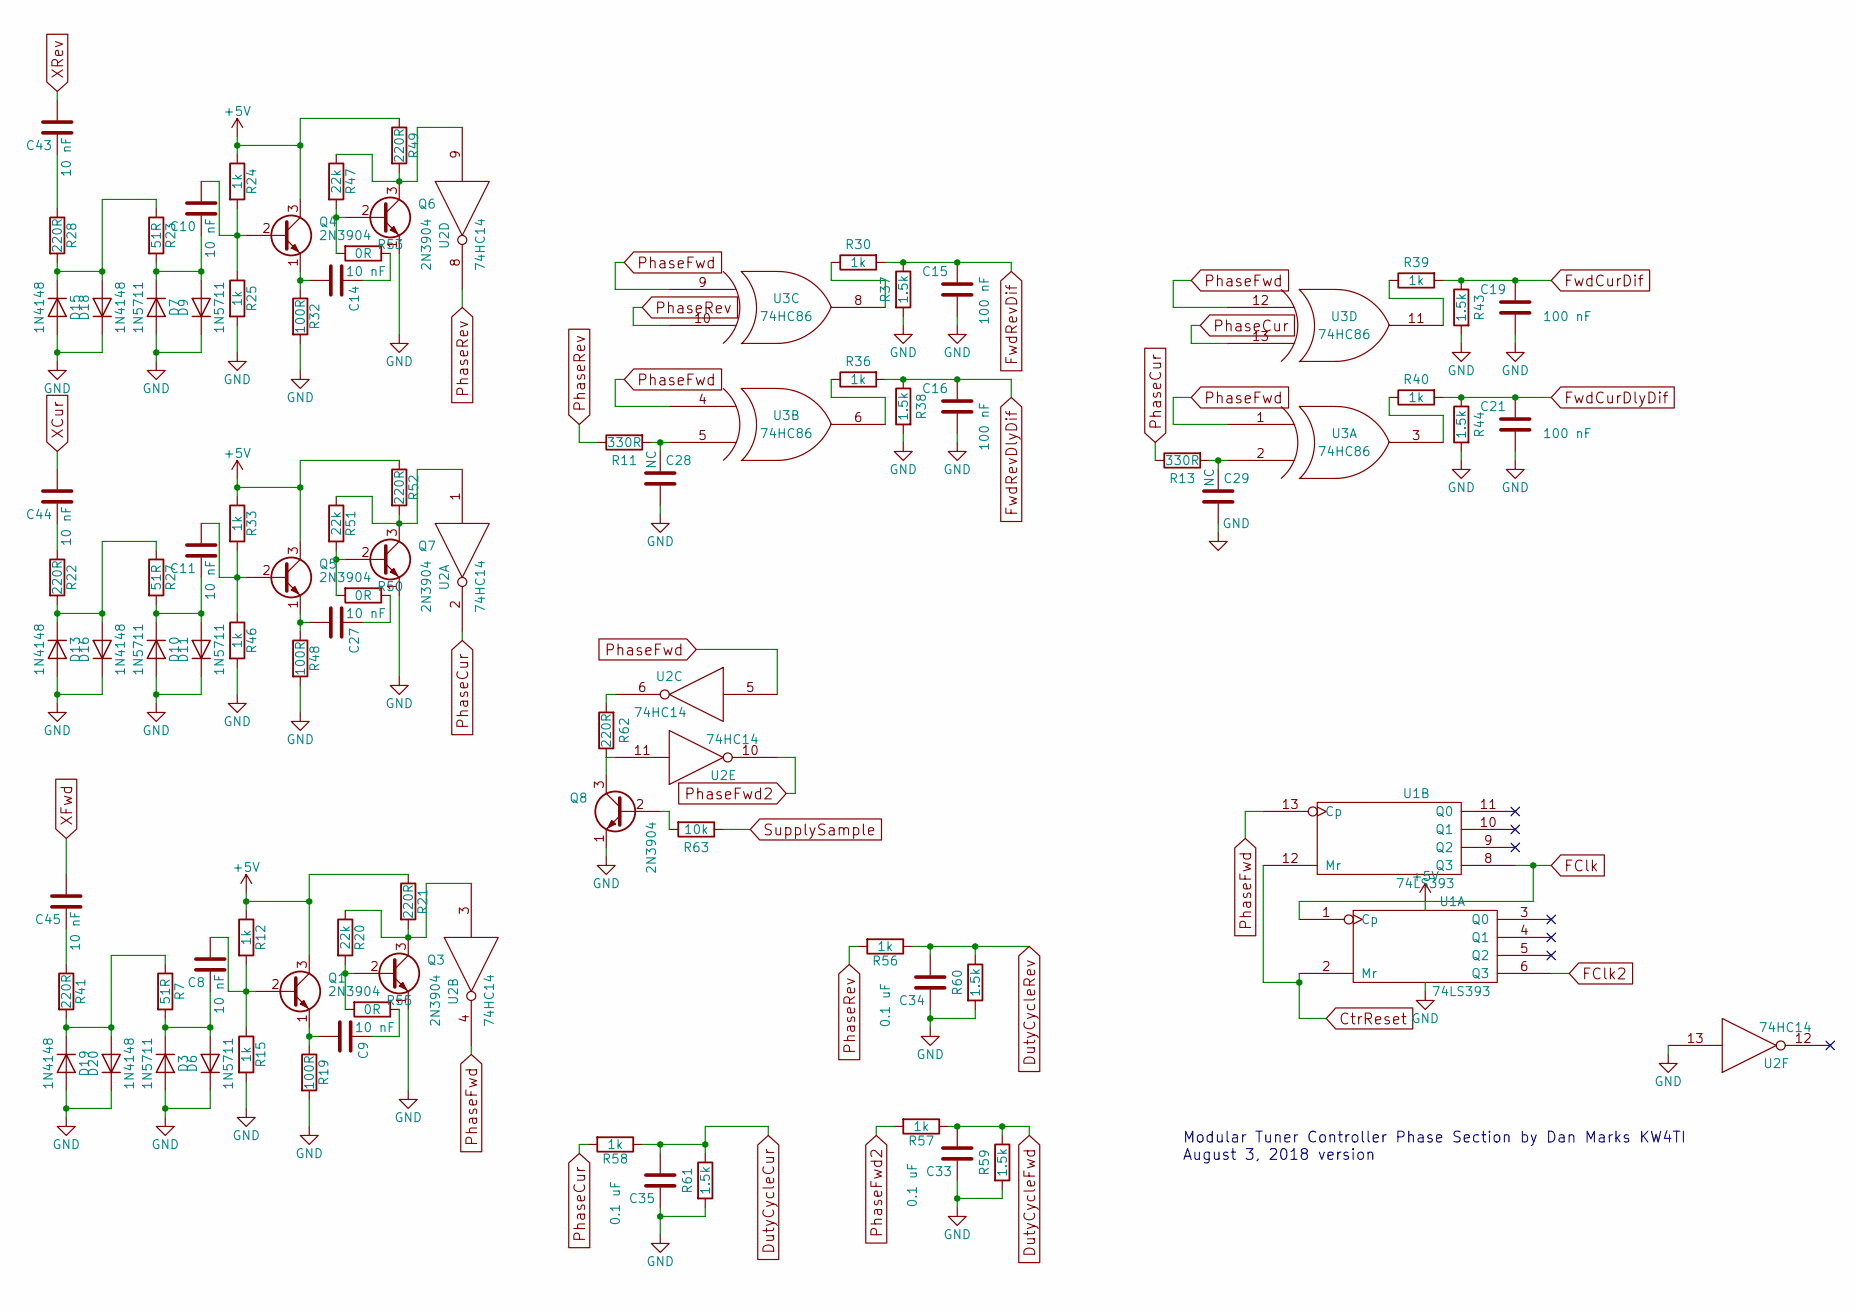
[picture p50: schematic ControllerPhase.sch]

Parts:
C8, C9, C10, C11, C14, C27, C43, C44, C45: 10 nF; C_Disc_D5.0mm_W2.5mm_P2.50mm
C15, C16, C19, C21: 100 nF; C_Disc_D5.0mm_W2.5mm_P5.00mm
C28, C29: NC; C_Disc_D5.0mm_W2.5mm_P5.00mm
C33, C34, C35: 0.1 uF; C_Disc_D5.0mm_W2.5mm_P5.00mm
D3, D6, D7, D9, D10, D11: 1N5711; D_DO-35_SOD27_P7.62mm_Horizontal
D13, D15, D16, D18, D19, D20: 1N4148; D_DO-35_SOD27_P7.62mm_Horizontal
Q1, Q3, Q4, Q5, Q6, Q7, Q8: 2N3904; TO-92_Molded_Narrow
R7, R23, R27: 51R; R_Axial_DIN0207_L6.3mm_D2.5mm_P7.62mm_Horizontal
R11, R13: 330R; R_Axial_DIN0207_L6.3mm_D2.5mm_P7.62mm_Horizontal
R12, R15, R24, R25, R30, R33, R36, R39, R40, R46, R56, R57, R58: 1k; R_Axial_DIN0207_L6.3mm_D2.5mm_P7.62mm_Horizontal
R19, R32, R48: 100R; R_Axial_DIN0207_L6.3mm_D2.5mm_P7.62mm_Horizontal
R20, R47, R51: 22k; R_Axial_DIN0207_L6.3mm_D2.5mm_P7.62mm_Horizontal
R21, R22, R28, R41, R49, R52, R62: 220R; R_Axial_DIN0207_L6.3mm_D2.5mm_P7.62mm_Horizontal
R37, R38, R43, R44, R59, R60, R61: 1.5k; R_Axial_DIN0207_L6.3mm_D2.5mm_P7.62mm_Horizontal
R50, R53, R55: 0R; R_Axial_DIN0207_L6.3mm_D2.5mm_P7.62mm_Horizontal
R63: 10k; R_Axial_DIN0207_L6.3mm_D2.5mm_P7.62mm_Horizontal
U1: 74LS393; DIP-14_W7.62mm_Socket
U2: 74HC14; DIP-14_W7.62mm_Socket
U3: 74HC86; DIP-14_W7.62mm_Socket

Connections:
CtrReset: U1.2 (Mr), U1.12 (Mr); also elsewhere on the board
DutyCycleCur: C35.2, R58.1, R61.1; also elsewhere on the board
DutyCycleFwd: C33.2, R57.1, R59.1; also elsewhere on the board
DutyCycleRev: C34.2, R56.1, R60.1; also elsewhere on the board
FClk2: U1.6 (Q3); also elsewhere on the board
FwdCurDif: C19.1, R39.2, R43.1; also elsewhere on the board
FwdCurDlyDif: C21.1, R40.2, R44.1; also elsewhere on the board
FwdRevDif: C15.1, R30.2, R37.1; also elsewhere on the board
FwdRevDlyDif: C16.1, R36.2, R38.1; also elsewhere on the board
GND: C15.2, C16.2, C19.2, C21.2, C28.2, C29.2, C33.1, C34.1, C35.1, D3.2 (A), D6.1 (K), D7.2 (A), D9.1 (K), D10.2 (A), D11.1 (K), D13.2 (A), D15.2 (A), D16.1 (K), D18.1 (K), D19.2 (A), D20.1 (K), Q3.1 (E), Q6.1 (E), Q7.1 (E), Q8.1 (E), R15.2, R19.2, R25.2, R32.2, R37.2, R38.2, R43.2, R44.2, R46.2, R48.2, R59.2, R60.2, R61.2, U1.7 (GND), U2.7 (GND), U2.13, U3.7 (GND); also elsewhere on the board
unnamed: C8.1, D3.1 (K), D6.2 (A), R7.2
unnamed: C8.2, Q1.2 (B), R12.2, R15.1
unnamed: C9.1, R55.1
unnamed: C9.2, Q1.1 (E), R19.1
unnamed: C10.1, D7.1 (K), D9.2 (A), R23.2
unnamed: C10.2, Q4.2 (B), R24.2, R25.1
unnamed: C11.1, D10.1 (K), D11.2 (A), R27.2
unnamed: C11.2, Q5.2 (B), R33.2, R46.1
unnamed: C14.1, R53.1
unnamed: C14.2, Q4.1 (E), R32.1
unnamed: C27.1, R50.1
unnamed: C27.2, Q5.1 (E), R48.1
unnamed: C28.1, R11.2, U3.5 (IN2)
unnamed: C29.1, R13.2, U3.2 (IN2)
unnamed: C43.1, R28.1
unnamed: C44.1, R22.1
unnamed: C45.1, R41.1
unnamed: D13.1 (K), D16.2 (A), R22.2, R27.1
unnamed: D15.1 (K), D18.2 (A), R23.1, R28.2
unnamed: D19.1 (K), D20.2 (A), R7.1, R41.2
unnamed: Q3.2 (B), R20.2, R55.2
unnamed: Q3.3 (C), R20.1, R21.2, U2.3
unnamed: Q6.2 (B), R47.2, R53.2
unnamed: Q6.3 (C), R47.1, R49.2, U2.9
unnamed: Q7.2 (B), R50.2, R51.2
unnamed: Q7.3 (C), R51.1, R52.2, U2.1
unnamed: Q8.2 (B), R63.2
unnamed: Q8.3 (C), R62.1, U2.11
unnamed: R30.1, U3.8 (OUT)
unnamed: R36.1, U3.6 (OUT)
unnamed: R39.1, U3.11 (OUT)
unnamed: R40.1, U3.3 (OUT)
unnamed: R62.2, U2.6
PhaseCur: R13.1, R58.2, U2.2, U3.13 (IN2)
PhaseFwd: U1.13 (Cp), U2.4, U2.5, U3.1 (IN1), U3.4 (IN1), U3.9 (IN1), U3.12 (IN1)
PhaseFwd2: R57.2, U2.10
PhaseRev: R11.1, R56.2, U2.8, U3.10 (IN2)
SupplySample: R63.1; also elsewhere on the board
XCur: C44.2; also elsewhere on the board
XFwd: C45.2; also elsewhere on the board
XRev: C43.2; also elsewhere on the board

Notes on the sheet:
Modular Tuner Controller Phase Section by Dan Marks KW4TI August 3, 2018 version

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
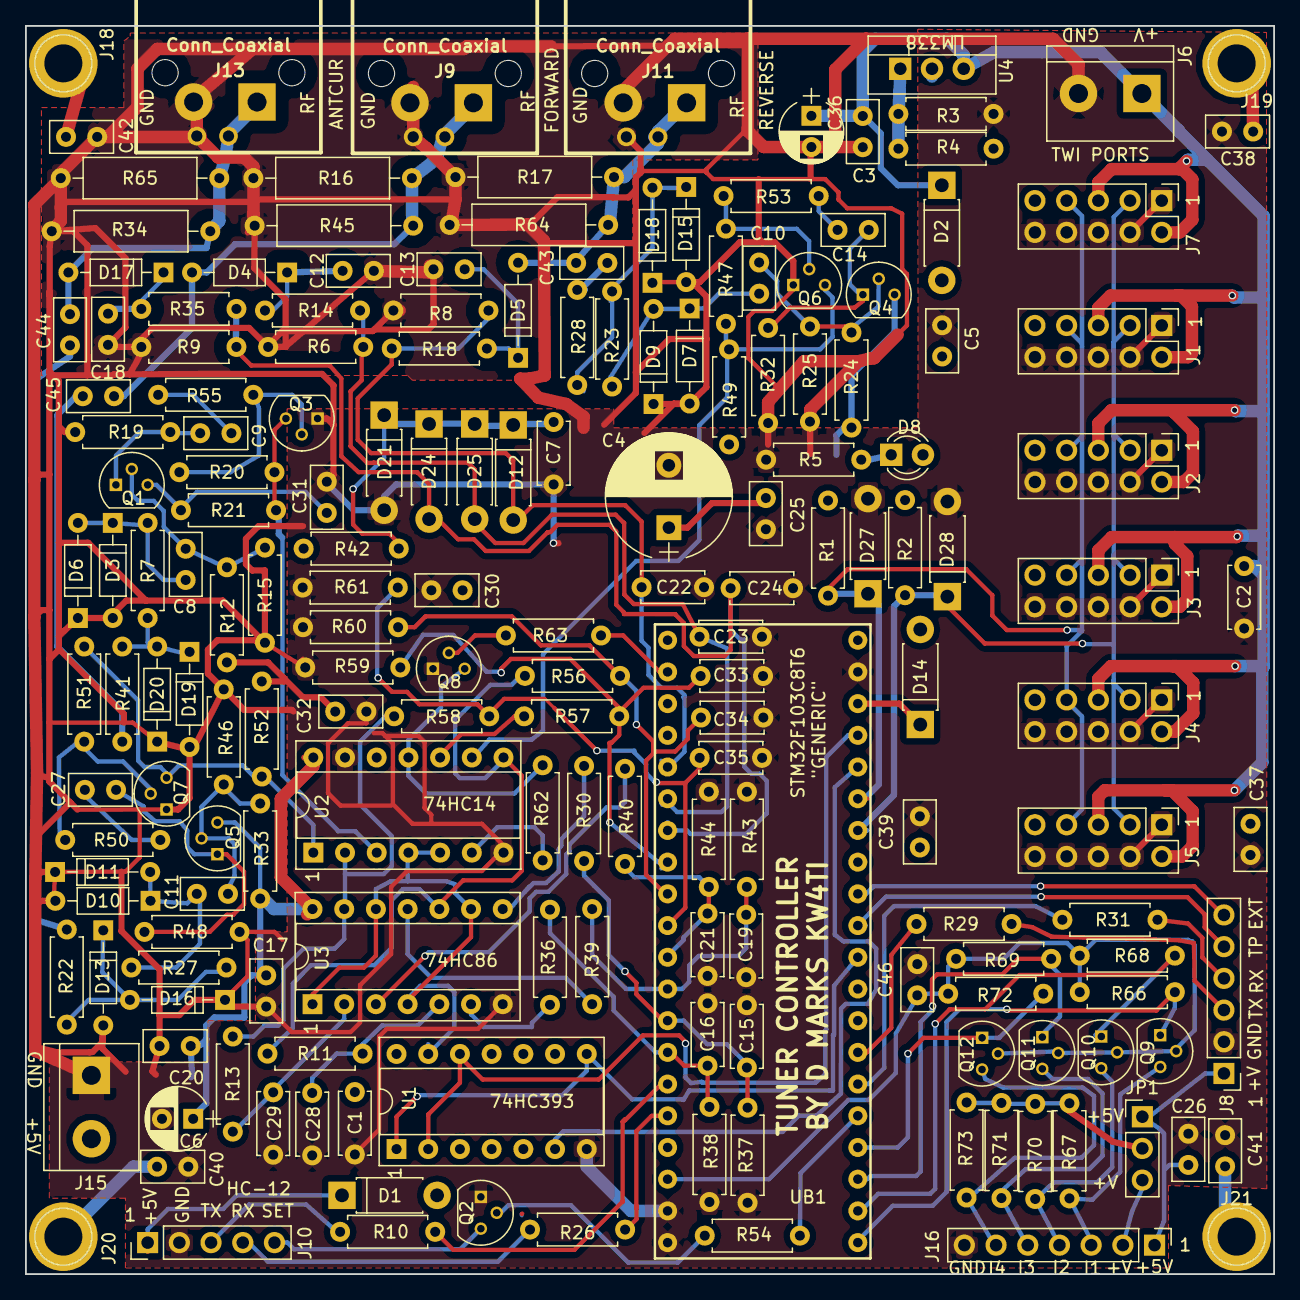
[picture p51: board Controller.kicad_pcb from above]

Board: 2 copper layers, 100.0 x 100.0 mm, 180 parts (0 on the bottom side), 95 nets.

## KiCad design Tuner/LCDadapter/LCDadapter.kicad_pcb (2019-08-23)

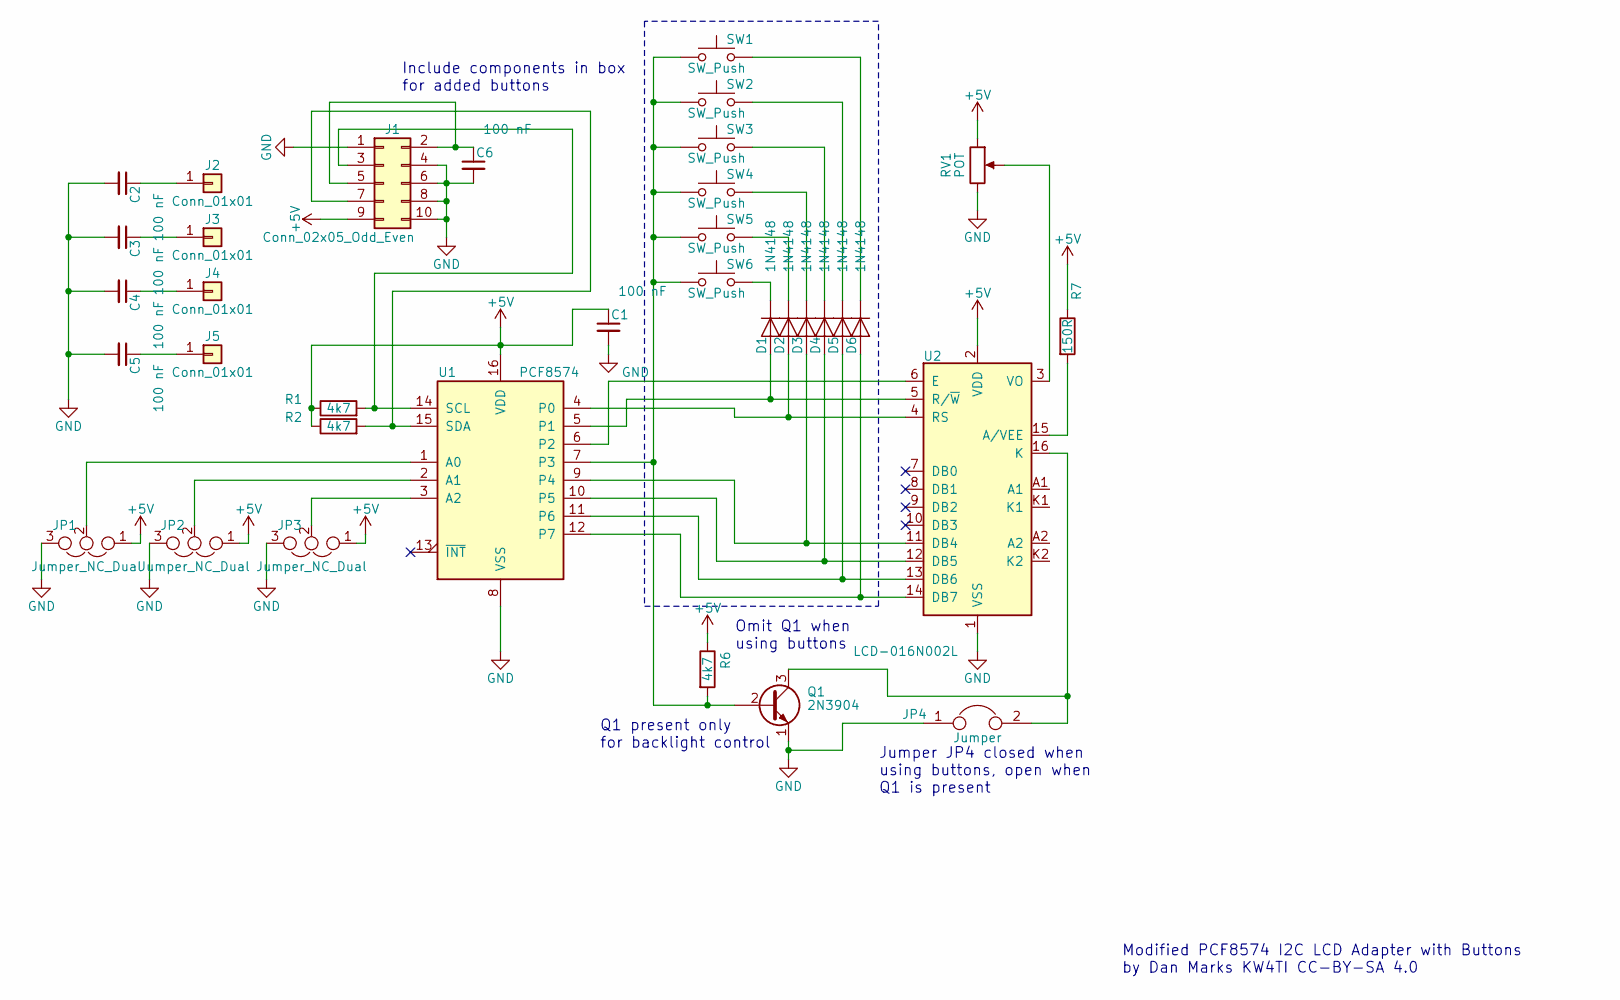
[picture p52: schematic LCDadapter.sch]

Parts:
C1, C2, C3, C4, C5, C6: 100 nF; C_Disc_D5.0mm_W2.5mm_P2.50mm
D1, D2, D3, D4, D5, D6: 1N4148; D_DO-35_SOD27_P7.62mm_Horizontal
J1: Conn_02x05_Odd_Even; Pin_Header_Straight_2x05_Pitch2.54mm
J2, J3, J4, J5: Conn_01x01; 1pin
JP1, JP2, JP3: Jumper_NC_Dual; Pin_Header_Straight_1x03_Pitch2.54mm
JP4: Jumper; Pin_Header_Straight_1x02_Pitch2.54mm
Q1: 2N3904; TO-92_Molded_Narrow
R1, R2, R6: 4k7; R_Axial_DIN0207_L6.3mm_D2.5mm_P7.62mm_Horizontal
R7: 150R; R_Axial_DIN0207_L6.3mm_D2.5mm_P7.62mm_Horizontal
RV1: POT; Potentiometer_Triwood_RM-065
SW1, SW2, SW3, SW4, SW5, SW6: SW_Push; SW_PUSH_6mm_h4.3mm
U1: PCF8574; DIP-16_W7.62mm_Socket
U2: LCD-016N002L; Pin_Header_Straight_1x16_Pitch2.54mm

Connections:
+5V: C1.1, J1.9, JP1.1, JP2.1, JP3.1, R1.1, R2.1, R6.1, R7.1, RV1.1, U1.16 (VDD), U2.2 (VDD)
GND: C1.2, C2.2, C3.2, C4.2, C5.2, C6.2, J1.1, J1.4, J1.6, J1.8, J1.10, JP1.3, JP2.3, JP3.3, JP4.1, Q1.1 (E), RV1.3, U1.8 (VSS), U2.1 (VSS)
unnamed: C2.1, J2.1
unnamed: C3.1, J3.1
unnamed: C4.1, J4.1
unnamed: C5.1, J5.1
unnamed: C6.1, J1.2, J1.5
unnamed: D1.1 (K), SW6.2
unnamed: D1.2 (A), U1.5 (P1), U2.5 (R/~W)
unnamed: D2.1 (K), SW5.2
unnamed: D2.2 (A), U1.4 (P0), U2.4 (RS)
unnamed: D3.1 (K), SW4.2
unnamed: D3.2 (A), U1.9 (P4), U2.11 (DB4)
unnamed: D4.1 (K), SW3.2
unnamed: D4.2 (A), U1.10 (P5), U2.12 (DB5)
unnamed: D5.1 (K), SW2.2
unnamed: D5.2 (A), U1.11 (P6), U2.13 (DB6)
unnamed: D6.1 (K), SW1.2
unnamed: D6.2 (A), U1.12 (P7), U2.14 (DB7)
unnamed: J1.3, R1.2, U1.14 (SCL)
unnamed: J1.7, R2.2, U1.15 (SDA)
unnamed: JP1.2, U1.1 (A0)
unnamed: JP2.2, U1.2 (A1)
unnamed: JP3.2, U1.3 (A2)
unnamed: JP4.2, Q1.3 (C), U2.16 (K)
unnamed: Q1.2 (B), R6.2, SW1.1, SW2.1, SW3.1, SW4.1, SW5.1, SW6.1, U1.7 (P3)
unnamed: R7.2, U2.15 (A/VEE)
unnamed: RV1.2, U2.3 (VO)
unnamed: U1.6 (P2), U2.6 (E)

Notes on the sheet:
Modified PCF8574 I2C LCD Adapter with Buttons by Dan Marks KW4TI CC-BY-SA 4.0
Omit Q1 when using buttons
Jumper JP4 closed when using buttons, open when Q1 is present
Q1 present only for backlight control
Include components in box for added buttons

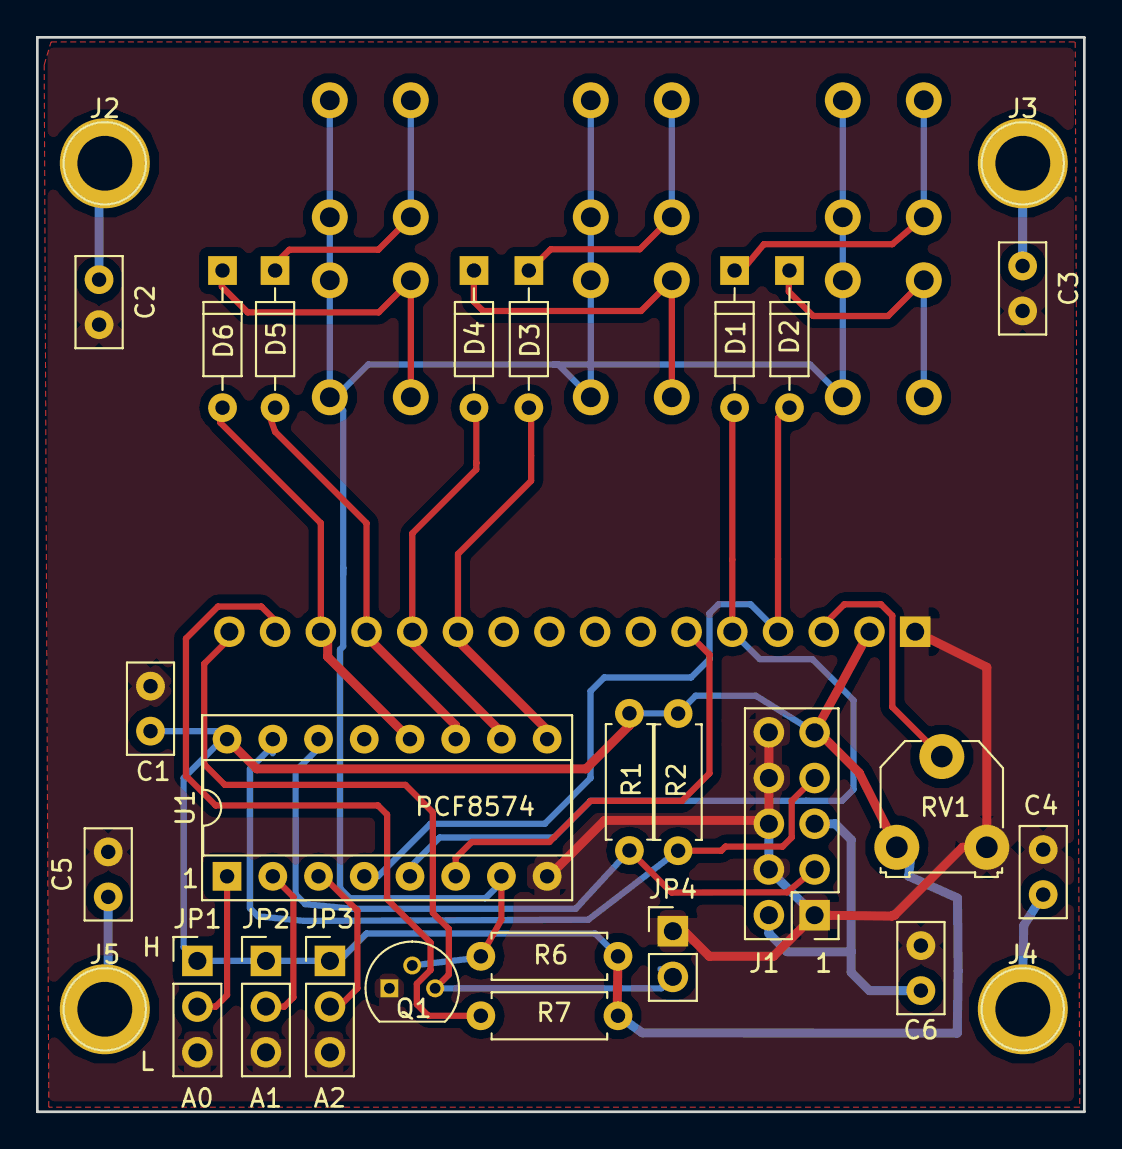
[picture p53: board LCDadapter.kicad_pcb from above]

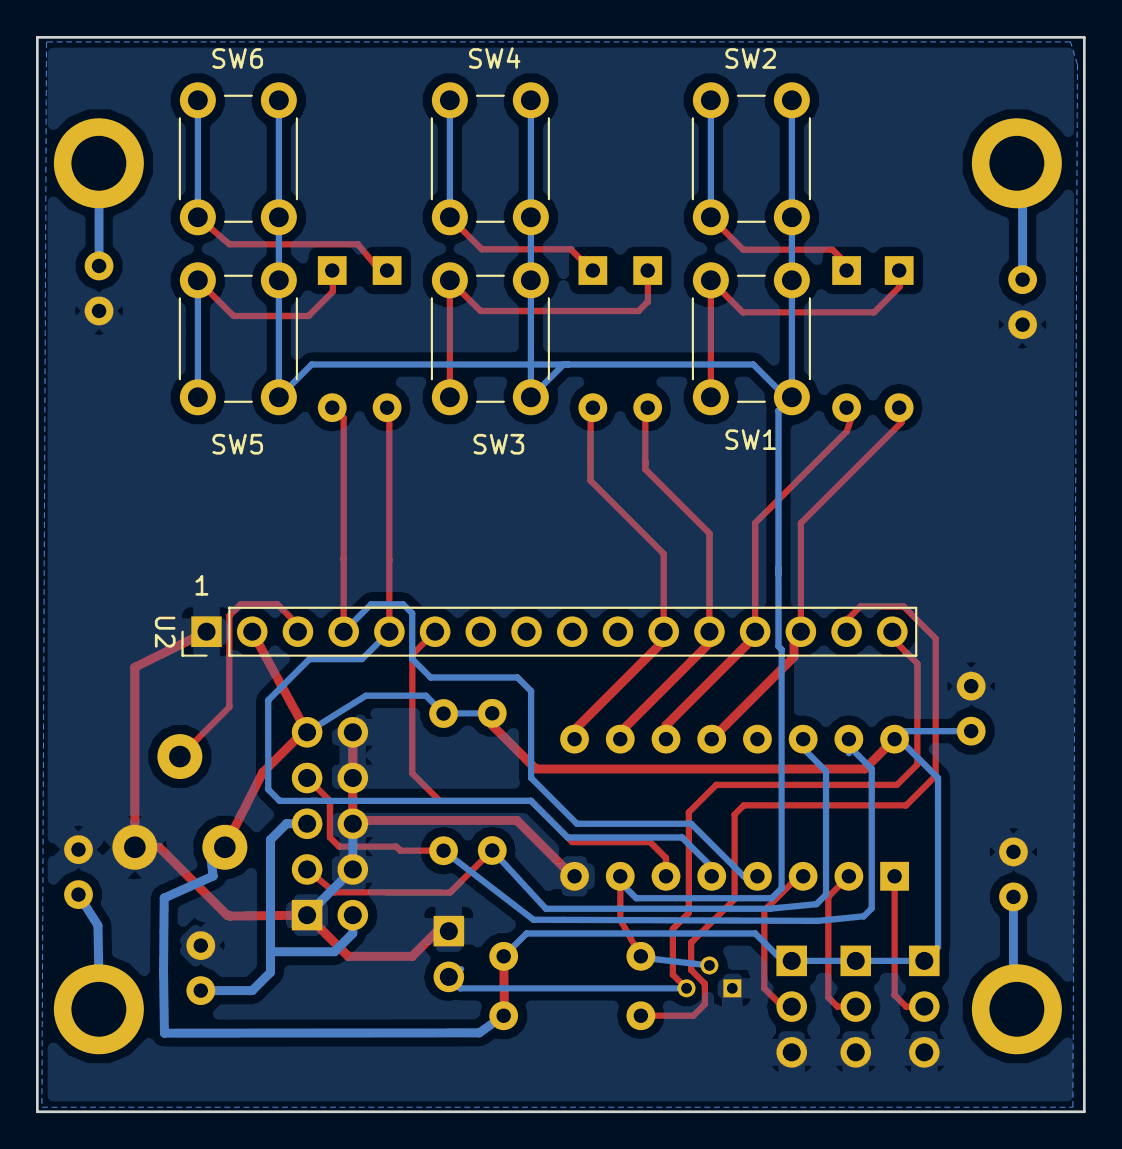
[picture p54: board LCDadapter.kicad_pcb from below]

Board: 2 copper layers, 58.2 x 59.7 mm, 35 parts (7 on the bottom side), 29 nets.

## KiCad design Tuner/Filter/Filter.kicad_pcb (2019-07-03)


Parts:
C1, C2, C3, C4, C5, C6, C7, C8, C9, C10, C11, C12, C13, C14, C15, C16, C17, C18: C_Small; C_Disc_SMD
C19, C20, C21, C22, C37, C38: 100 nF; C_Disc_D5.0mm_W2.5mm_P2.50mm
C23: 100 uF; CP_Radial_D6.3mm_P2.50mm
C24, C33, C34, C35: 10 nF; C_Disc_D5.0mm_W2.5mm_P2.50mm
C25, C26: C_Small; C_Disc_D5.0mm_W2.5mm_P2.50mm
C27, C28, C29, C30, C31, C32: C; C_Disc_D5.0mm_W2.5mm_P2.50mm
C36: 10 nF; C_Disc_D5.0mm_W2.5mm_P5.00mm
J1, J3: Conn_Coaxial; bnc_90_1-1337543-0
J2, J5: Conn_01x02; TerminalBlock_bornier-2_P5.08mm
J4: Conn_02x05_Odd_Even; Pin_Header_Straight_2x05_Pitch2.54mm
J6, J7, J8, J9: Conn_01x01; 1pin
JP1, JP2, JP3, JP4: Jumper_NC_Dual; Pin_Header_Straight_1x03_Pitch2.54mm
L1, L2, L3, L4, L5, L6, L7, L8, L9, L10, L11, L12: L_Small; L_Toroid_Vertical_L13.0mm_W6.5mm_P5.60mm
L13, L14, L15, L16, L17, L18, L19, L20: 100 uH; L_Axial_L5.3mm_D2.2mm_P7.62mm_Horizontal_Vishay_IM-1
R1, R2: 2.2k; R_Axial_DIN0207_L6.3mm_D2.5mm_P7.62mm_Horizontal
RLY1, RLY2, RLY3, RLY4, RLY5, RLY6: DPDTRelay; G2VRelay
U1: MCP23008; DIP-18_W7.62mm_Socket
U3: ULN2803A; DIP-18_W7.62mm_Socket

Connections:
+5V: C20.2, C22.2, C23.1, J4.9, JP1.3, JP2.3, JP3.3, JP4.3, R1.1, R2.1, U1.6 (~RESET), U1.18 (VCC)
EXTPWR: C38.2, JP1.2, L20.1
GND: C19.2, C20.1, C21.1, C22.1, C23.2, C24.2, C25.2, C26.2, C33.2, C34.2, C35.2, C38.1, J4.1, J4.4, J4.6, J4.8, J4.10, JP2.1, JP3.1, JP4.1, L19.1, U1.9 (GND)
INRF: J1.1 (In), J2.1, RLY1.2 (Pole), RLY2.2 (Pole), RLY3.2 (Pole), RLY4.2 (Pole), RLY5.2 (Pole), RLY6.2 (Pole)
unnamed: C1.1, L1.1, RLY1.8 (NO)
unnamed: C2.1, L2.1, RLY2.8 (NO)
unnamed: C3.1, L3.1, RLY3.8 (NO)
unnamed: C4.1, L4.1, RLY4.8 (NO)
unnamed: C5.1, L5.1, RLY5.8 (NO)
unnamed: C6.1, L6.1, RLY6.8 (NO)
unnamed: C7.1, L1.2, L7.1
unnamed: C8.1, L2.2, L8.1
unnamed: C9.1, L3.2, L9.1
unnamed: C10.1, L4.2, L10.1
unnamed: C11.1, L5.2, L11.1
unnamed: C12.1, L6.2, L12.1
unnamed: C13.1, L7.2, RLY1.4 (NO)
unnamed: C14.1, L8.2, RLY2.4 (NO)
unnamed: C15.1, L9.2, RLY3.4 (NO)
unnamed: C16.1, L10.2, RLY4.4 (NO)
unnamed: C17.1, L11.2, RLY5.4 (NO)
unnamed: C18.1, L12.2, RLY6.4 (NO)
unnamed: C19.1, J9.1
unnamed: C21.2, J4.2, J4.5, JP1.1
unnamed: C24.1, L13.1, U1.10 (GPB0)
unnamed: C25.1, L14.1, U1.11 (GPB1)
unnamed: C26.1, L15.1, U1.12 (GPB2)
unnamed: C27.1, RLY1.5 (Coil), U3.18 (O1)
unnamed: C28.1, RLY2.5 (Coil), U3.17 (O2)
unnamed: C29.1, RLY5.5 (Coil), U3.14 (O5)
unnamed: C30.1, RLY6.5 (Coil), U3.13 (O6)
unnamed: C31.1, RLY3.5 (Coil), U3.16 (O3)
unnamed: C32.1, RLY4.5 (Coil), U3.15 (O4)
unnamed: C33.1, L16.1, U1.13 (GPB3)
unnamed: C34.1, L17.1, U1.14 (GPB4)
unnamed: C35.1, L18.1, U1.15 (GPB5)
unnamed: C37.1, J6.1
unnamed: J3.1 (In), J5.1, RLY1.6 (Pole), RLY2.6 (Pole), RLY3.6 (Pole), RLY4.6 (Pole), RLY5.6 (Pole), RLY6.6 (Pole)
unnamed: JP2.2, U1.5 (A0)
unnamed: JP3.2, U1.4 (A1)
unnamed: JP4.2, U1.3 (A2)
unnamed: L13.2, U3.1 (I1)
unnamed: L14.2, U3.2 (I2)
unnamed: L15.2, U3.3 (I3)
unnamed: L16.2, U3.4 (I4)
unnamed: L17.2, U3.5 (I5)
unnamed: L18.2, U3.6 (I6)
RFGND: C1.2, C2.2, C3.2, C4.2, C5.2, C6.2, C7.2, C8.2, C9.2, C10.2, C11.2, C12.2, C13.2, C14.2, C15.2, C16.2, C17.2, C18.2, J1.2 (Ext), J2.2, J3.2 (Ext), J5.2, J7.1, J8.1
RLYGND: C36.2, L19.2, U3.7 (I7), U3.8 (I8), U3.9 (GND)
RLYPWR: C27.2, C28.2, C29.2, C30.2, C31.2, C32.2, C36.1, C37.2, L20.2, RLY1.1 (Coil), RLY2.1 (Coil), RLY3.1 (Coil), RLY4.1 (Coil), RLY5.1 (Coil), RLY6.1 (Coil), U3.10 (COM)
SCL: J4.3, R1.2, U1.1 (SCL)
SDA: J4.7, R2.2, U1.2 (SDA)

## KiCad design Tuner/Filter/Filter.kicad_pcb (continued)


Board: 2 copper layers, 100.0 x 100.0 mm, 81 parts (0 on the bottom side), 52 nets.

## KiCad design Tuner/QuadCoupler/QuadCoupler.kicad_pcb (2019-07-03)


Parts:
C1, C2, C3, C4, C14, C19: 10 nF; C_Disc_D5.0mm_W2.5mm_P5.00mm
C5, C6, C7, C11, C12, C13, C15, C18, C21, C23, C27, C28, C29: NC; C_Disc_D5.0mm_W2.5mm_P5.00mm
C8, C31: 68 pF 1 kV; C_Disc_D5.0mm_W2.5mm_P5.00mm
C9, C10, C30, C32: 47 pF 1 kV; C_Disc_D5.0mm_W2.5mm_P5.00mm
C16, C17, C20, C22, C24, C25, C26: 10 nF 1 kV; C_Disc_D5.0mm_W2.5mm_P5.00mm
D1, D2, D3, D4, D5, D6, D7, D8: 1N4148; D_DO-35_SOD27_P7.62mm_Horizontal
J1, J7, J8, J9, J11, J12, J13, J14, J15, J16, J17, J21, J22, J23, J24: Conn_01x01; 1pin
J2, J3, J4, J5, J6: Conn_Coaxial; bnc_90_1-1337543-0_pad_combo
J10, J19: Conn_01x02; TerminalBlock_bornier-2_P5.08mm
JP1, JP2, JP3, JP4, JP5, JP6, JP7, JP8, JP9, JP10: Jumper_NC_Small; Pin_Header_Straight_1x02_Pitch2.54mm
R1, R2, R3, R4, R5, R6, R9, R10, R11, R12, R13, R14, R21, R22, R23, R24, R25, R26, R27, R28, R29, R30, R31, R32, R33, R34, R35, R36, R37, R38: 1k; R_Axial_DIN0411_L9.9mm_D3.6mm_P12.70mm_Horizontal
R7, R16, R18, R19: 100k; R_Axial_DIN0207_L6.3mm_D2.5mm_P7.62mm_Horizontal
R8, R15, R17, R20: 10k; R_Axial_DIN0207_L6.3mm_D2.5mm_P7.62mm_Horizontal
TR1, TR2, TR3, TR4, TR5, TR6: autotransformer

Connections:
GND: C1.2, C2.2, C3.2, C4.2, C5.2, C6.2, C7.2, C8.2, C9.2, C10.2, C14.2, C19.2, C27.2, C28.2, C29.2, C30.2, C31.2, C32.2, J2.2 (Ext), J3.2 (Ext), J4.2 (Ext), J5.2 (Ext), J6.2 (Ext), J10.2, J12.1, J14.1, J19.2, J21.1, J22.1, J23.1, J24.1, JP1.2, JP2.2, JP7.2, JP8.2, R8.1, R15.1, R17.1, R20.1, TR1.1, TR3.1, TR4.1
unnamed: C1.1, JP1.1, R15.2, R18.1
unnamed: C2.1, JP2.1, R16.1, R17.2
unnamed: C3.1, JP7.1, R7.1, R8.2
unnamed: C4.1, JP8.1, R19.1, R20.2
unnamed: C10.1, C30.1, TR4.2, TR6.2
unnamed: C6.1, C11.1, C28.1, JP3.1, R1.1, R2.1, R3.1, R4.1, R27.1, R28.1, R29.1, R30.1, R31.1, R32.1, TR2.3, TR4.3
unnamed: C5.1, C11.2, C27.1, JP10.2, R1.2, R2.2, R3.2, R4.2, R27.2, R28.2, R29.2, R30.2, R31.2, R32.2, TR2.1, TR3.3
unnamed: C12.1, C18.2, C23.2, JP5.1, R5.1, R9.1, R11.1, R13.1, R21.1, R22.1, R23.1, R24.1, R25.1, R26.1, TR5.3
unnamed: C12.2, C16.2, C22.2, JP9.1, R5.2, R9.2, R11.2, R13.2, R21.2, R22.2, R23.2, R24.2, R25.2, R26.2, TR5.1
unnamed: C13.1, C17.2, C20.2, JP6.2, R6.1, R10.1, R12.1, R14.1, R33.1, R34.1, R35.1, R36.1, R37.1, R38.1, TR6.3
unnamed: C13.2, C15.2, C21.2, JP4.2, R6.2, R10.2, R12.2, R14.2, R33.2, R34.2, R35.2, R36.2, R37.2, R38.2, TR6.1
unnamed: C14.1, C19.1, J1.1, J7.1, J8.1, J9.1, J10.1, J19.1
unnamed: C15.1, C21.1, J4.1 (In), J17.1
unnamed: C16.1, C22.1, J6.1 (In), J15.1
unnamed: C17.1, C20.1, J2.1 (In), J11.1
unnamed: C18.1, C23.1, J5.1 (In), J13.1
unnamed: C7.1, C24.1, C25.1, C26.1, C29.1, TR1.3
unnamed: C24.2, C25.2, C26.2, J3.1 (In), J16.1
unnamed: C8.1, C31.1, TR1.2, TR2.2
unnamed: C9.1, C32.1, TR3.2, TR5.2
unnamed: D1.1 (K), D4.2 (A)
unnamed: D1.2 (A), JP3.2, JP6.1
unnamed: D2.1 (K), D7.2 (A)
unnamed: D2.2 (A), JP5.2
unnamed: D3.1 (K), D5.2 (A)
unnamed: D3.2 (A), JP4.1
unnamed: D4.1 (K), R18.2
unnamed: D5.1 (K), R16.2
unnamed: D6.1 (K), D8.2 (A)
unnamed: D6.2 (A), JP9.2, JP10.1
unnamed: D7.1 (K), R7.2
unnamed: D8.1 (K), R19.2

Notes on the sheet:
1:1 bifilar autotransformer
14:10 P3:P2 trifilar 1.96:1 impedance autotransformer 5 turns of trifilar wire on two FT82-43 cores, the final turn removed
QUAD POWER COUPLER BY DAN MARKS KW4TI CC-BY-SA 4.0


Board: 2 copper layers, 100.0 x 100.0 mm, 116 parts (0 on the bottom side), 33 nets.

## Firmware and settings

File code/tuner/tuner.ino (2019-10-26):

/*
 *  Antenna Tuner STM32duino project
 */

/*
 * Copyright (c) 2018 Daniel Marks

This software is provided 'as-is', without any express or implied
warranty. In no event will the authors be held liable for any damages
arising from the use of this software.

Permission is granted to anyone to use this software for any purpose,
including commercial applications, and to alter it and redistribute it
freely, subject to the following restrictions:

1. The origin of this software must not be misrepresented; you must not
   claim that you wrote the original software. If you use this software
   in a product, an acknowledgment in the product documentation would be
   appreciated but is not required.
2. Altered source versions must be plainly marked as such, and must not be
   misrepresented as being the original software.
3. This notice may not be removed or altered from any source distribution.
 */

#include "tuner.h"
#include "swrmeter.h"
#include "FrequencyCounter.h"
#include "LNetwork.h"
#include "RelayModule.h"
#include "complex.h"
#include "debugmsg.h"
#include "mini-printf.h"
#include "tinycl.h"
#include "structconf.h"
#include "flashstruct.h"
#include "interface.h"
#include "consoleio.h"
#include "remote.h"

tuner_ready_state tuner_ready = TUNER_READY_STANDBY;
const char *tuner_state_string[3] = { "STANDBY", "FORCE TUNE", "DISABLED" };

const char *tuner_short_state_string[3] = { "SBY", "FTN", "DIS" };

unsigned int      last_update_tick;
int               current_memory = -1;
bool              needs_update = false;
bool              tuner_bypass_mode = true;
tunerr_condition  tunerr_last = TUNERR_SUCCESS;

const char *tuner_error_condition_string[5] = { "SUCCESS", "HIGH SWR", "POWER LOSS", "POWER HIGH", "ABORTED" };

swr_state last_swr_state = { 0.0f, 0.0f, 0.0f, 0.0f, 0.0f, 0.0f, Complex(0.0f, 0.0f), Complex(0.0f, 0.0f), 0.0f };

SWRMeter swrMeter;
FrequencyCounter freqCounter(PB9,16u,1,10000);

tuner_parameters tpar = { {"NONE"},         /* tune_label */
                          12.0f,            /* tune_power_calib */
                          0.5f,             /* tune_min_power */
                          15.0f,            /* tune_max_power */
                          0.2f,             /* tune_max_ref */
                          0.25f,            /* tune_return_thr */
                          1.05f,            /* tune_search_relaxation */
                          1,                /* tune_remote_channel_no */
                          1,                /* tune_remote_id */
                          10,               /* tune_search_khz_spacing */
                          0,                /* tune_rig_control */
#ifdef TUNER_BIG_RELAYS_DEFAULT
                          { 1, 2, 0, 0, 0, 0, 0, 0, 0, 0, 0, 0, 0, 0, 0, 0, 0, 0 },   /* tune_switchstate_bypass */
                          { 1, 2, 1, 2, 1, 0, 0, 0, 0, 0, 0, 0, 0, 0, 0, 0, 0, 0 },   /* tune_switchstate_1 */
                          { 1, 2, 1, 2, 1, 1, 0, 0, 0, 0, 0, 0, 0, 0, 0, 0, 0, 0 },   /* tune_switchstate_2 */
                          { 0, 0, 0, 0, 0, 0, 0, 0, 0, 0, 0, 0, 0, 0, 0, 0, 0, 0 },   /* tune_switchstate_3 */
                          { 0, 0, 0, 0, 0, 0, 0, 0, 0, 0, 0, 0, 0, 0, 0, 0, 0, 0 },   /* tune_switchstate_4 */
                          { 0, 0, 0, 0, 0, 0, 0, 0, 0, 0, 0, 0, 0, 0, 0, 0, 0, 0 },   /* tune_switchstate_5 */
                          { 0, 0, 0, 0, 0, 0, 0, 0, 0, 0, 0, 0, 0, 0, 0, 0, 0, 0 },   /* tune_switchstate_6 */
#endif
#ifdef TUNER_SMALL_RELAYS_DEFAULT
                          { 1, 1, 0, 0, 0, 0, 0, 0, 0, 0, 0, 0, 0, 0, 0, 0, 0, 0 },   /* tune_switchstate_bypass */
                          { 1, 1, 1, 2, 1, 0, 0, 0, 0, 0, 0, 0, 0, 0, 0, 0, 0, 0 },   /* tune_switchstate_1 */
                          { 1, 1, 1, 2, 1, 1, 0, 0, 0, 0, 0, 0, 0, 0, 0, 0, 0, 0 },   /* tune_switchstate_2 */
                          { 0, 0, 0, 0, 0, 0, 0, 0, 0, 0, 0, 0, 0, 0, 0, 0, 0, 0 },   /* tune_switchstate_3 */
                          { 0, 0, 0, 0, 0, 0, 0, 0, 0, 0, 0, 0, 0, 0, 0, 0, 0, 0 },   /* tune_switchstate_4 */
                          { 0, 0, 0, 0, 0, 0, 0, 0, 0, 0, 0, 0, 0, 0, 0, 0, 0, 0 },   /* tune_switchstate_5 */
                          { 0, 0, 0, 0, 0, 0, 0, 0, 0, 0, 0, 0, 0, 0, 0, 0, 0, 0 },   /* tune_switchstate_6 */
#endif

};

const structure_entry tuner_parameter_fields[18] =
{ { "LABEL",           STRUCTCONF_STRING,     offsetof(tuner_parameters,tune_label), sizeof(tpar.tune_label), STRUCTCONF_INTMIN, STRUCTCONF_INTMAX, NULL },
  { "POWERCALIB",      STRUCTCONF_FLOAT,      offsetof(tuner_parameters,tune_power_calib), 1, 0, STRUCTCONF_INTMAX,  },
  { "MINTUNINGPOWER",  STRUCTCONF_FLOAT,      offsetof(tuner_parameters,tune_min_power), 1, 0,  STRUCTCONF_INTMAX, NULL },
  { "MAXTUNINGPOWER",  STRUCTCONF_FLOAT,      offsetof(tuner_parameters,tune_max_power), 1, 0, STRUCTCONF_INTMAX, NULL },
  { "MAXREFLECTION",   STRUCTCONF_FLOAT,      offsetof(tuner_parameters,tune_max_ref), 1, 0, 1, NULL },
  { "RETUNETHRESHOLD", STRUCTCONF_FLOAT,      offsetof(tuner_parameters,tune_retune_thr), 1, 0, 1, NULL },
  { "SEARCHRELAXATION",STRUCTCONF_FLOAT,      offsetof(tuner_parameters,tune_search_relaxation), 1, 1, 2, NULL },
  { "REMOTECHANNELNO", STRUCTCONF_INT8,       offsetof(tuner_parameters,tune_remote_channel_no), 1, 0, 127, NULL },
  { "REMOTEID",        STRUCTCONF_INT8,       offsetof(tuner_parameters,tune_remote_id), 1, 0, 127, NULL },
  { "SEARCHKHZSPACING",STRUCTCONF_INT16,      offsetof(tuner_parameters,tune_search_khz_spacing), 1, 0, 100, NULL },
  { "RIGCONTROL",      STRUCTCONF_INT8,       offsetof(tuner_parameters,tune_rig_control), 1, 0, 3, "0=NONE 1=ICOM 2=KENWOOD 3=YAESU" },
  { "SWITCHBYPASS",    STRUCTCONF_INT8,       offsetof(tuner_parameters,tune_switchstate_bypass), TUNE_SWITCHSTATE_PER_STATE*3, 0, 255, NULL },
  { "SWITCHSTATE1",    STRUCTCONF_INT8,       offsetof(tuner_parameters,tune_switchstate_1), TUNE_SWITCHSTATE_PER_STATE*3, 0, 255, NULL },
  { "SWITCHSTATE2",    STRUCTCONF_INT8,       offsetof(tuner_parameters,tune_switchstate_2), TUNE_SWITCHSTATE_PER_STATE*3, 0, 255, NULL },
  { "SWITCHSTATE3",    STRUCTCONF_INT8,       offsetof(tuner_parameters,tune_switchstate_3), TUNE_SWITCHSTATE_PER_STATE*3, 0, 255, NULL },
  { "SWITCHSTATE4",    STRUCTCONF_INT8,       offsetof(tuner_parameters,tune_switchstate_4), TUNE_SWITCHSTATE_PER_STATE*3, 0, 255, NULL },
  { "SWITCHSTATE5",    STRUCTCONF_INT8,       offsetof(tuner_parameters,tune_switchstate_5), TUNE_SWITCHSTATE_PER_STATE*3, 0, 255, NULL },
  { "SWITCHSTATE6",    STRUCTCONF_INT8,       offsetof(tuner_parameters,tune_switchstate_6), TUNE_SWITCHSTATE_PER_STATE*3, 0, 255, NULL },
};

tuner_cache_entry tce[TUNER_CACHE_ENTRIES];
RelayModule relays[TUNER_MAX_RELAYS];

#define DEMCR           (*((volatile uint32_t *)0xE000EDFC))
#define DWT_CTRL        (*(volatile uint32_t *)0xe0001000)
#define CYCCNTENA       (1<<0)
#define DWT_CYCCNT      ((volatile uint32_t *)0xE0001004)
#define CPU_CYCLES      *DWT_CYCCNT
#define DEMCR_TRCENA    0x01000000

void initialize_tuner_cache_entries(void)
{
  memset(tce,'\000',sizeof(tce));
}

void restore_relays(void)
{
  int r;
  for (r=0;r<TUNER_MAX_RELAYS;r++)
     relays[r].setup();
}

void initialize_default_relays(void)
{
  memset(relays,'\000',sizeof(relays));
#ifdef TUNER_BIG_RELAYS_DEFAULT
  relays[0].setup(indRelay8);
  relays[1].setup(capRelay8);
#endif
#ifdef TUNER_SMALL_RELAYS_DEFAULT
  relays[0].setup(indRelay7);
  relays[1].setup(capRelay7);
#endif
}

static void initialize_cortex_m3_cycle_counter(void)
{
  DEMCR |= DEMCR_TRCENA; 
  *DWT_CYCCNT = 0; 
  DWT_CTRL |= CYCCNTENA;
}

void initialize_rig_control(void)
{
  switch (tpar.tune_rig_control)
  {
    case TUNER_RIG_CONTROL_ICOM:
        pinMode(PB13,INPUT);
        pinMode(PB12,OUTPUT);
        digitalWrite(PB12,HIGH);
        break;
    case TUNER_RIG_CONTROL_KENWOOD:
        break;
    case TUNER_RIG_CONTROL_YAESU:
        break;
  }
}

void check_i2c_active(void)
{
  pinMode(PB6,INPUT);
  pinMode(PB7,INPUT);
  while ((!digitalRead(PB6)) || (!digitalRead(PB7)))
  {
    console_println("Waiting for power");
    delay(250);
  }
  delay(250);
}

void setup() {
  check_i2c_active();
   afio_cfg_debug_ports(AFIO_DEBUG_NONE);
   afio_cfg_debug_ports(AFIO_DEBUG_SW_ONLY);
  initialize_cortex_m3_cycle_counter();
  // default debug messages off if on UART1 (might need it for rig)

  setDebugMsgMode(0);
  delay(250);
  swrMeter.setup();
  swrMeter.setImpedance(50.0f);
  freqCounter.setup();
  if (tuner_readstate(1))
     restore_relays();
  else
  { 
    initialize_tuner_cache_entries();
    initialize_default_relays();
  }
 tuner_set_bypass();
 Serial.begin(115200); 

#ifdef TUNER_USER_INTERFACE
  interface_initialize();
#endif
#ifdef TUNER_REMOTE_WIRELESS
  remote_initialize(tpar.tune_remote_channel_no, tpar.tune_remote_id);
#endif
  initialize_rig_control();
}

float adjust_pwr(float rawpwr)
{
  return tpar.tune_power_calib*rawpwr*rawpwr;
}

void tuner_set_state(tuner_ready_state p)
{
  tuner_ready = p;
}

tuner_ready_state tuner_get_state(void)
{
  return tuner_ready;
}

bool tuner_get_bypass(void)
{
  return tuner_bypass_mode;
}

const char *tuner_ready_string(tuner_ready_state p)
{
  return tuner_state_string[tuner_ready];
}

const char *tuner_ready_short_string(tuner_ready_state p)
{
  return tuner_short_state_string[tuner_ready];
}

int tune_cmd(int args, tinycl_parameter *tp, void *v)
{
  int p = tp[0].ti.i;
  if ((p<1)||(p>3))
  {
    console_println("Invalid tuner state");
  } else
  {
    tuner_set_state((tuner_ready_state) (p-1));
    console_print("Tune State: ");
    console_println(tuner_ready_string(tuner_get_state()));
  }
  return 1;
}

int debug_cmd(int args, tinycl_parameter *tp, void *v)
{
  int d = tp[0].ti.i;
  setDebugMsgMode(d);
  console_print("Debug State: ");
  console_println(d);
  return 1;
}

int test_relay_cmd(int args, tinycl_parameter *tp, void *v)
{
  int rlyno = tp[0].ti.i;
  int isswitch = tp[1].ti.i;
  int number = tp[2].ti.i;
  int setting = tp[3].ti.i;

  if ((rlyno < 1) || (rlyno > TUNER_MAX_RELAYS))
  {
    console_println("Invalid relay #");
    return 1;
  }
  RelayModule *rm = &relays[rlyno-1];
  if (!rm->isValidModule())
  {
    console_println("Invalid relay #");
    return 1;
  }  
  if (isswitch)
      rm->setSwitchState(number-1,setting);
  else
      rm->setRelayState(number-1,setting);
  return 1;
}

int setrly_cmd(int args, tinycl_parameter *tp, void *v)
{
  int rlyno = tp[0].ti.i;
  int rlyval = tp[1].ti.i;
  int method = tp[2].ti.i;
  console_print("Setting relay #");
  console_print(rlyno);
  console_print(" to value ");
  console_println(rlyval);
  int val;
  if ((rlyno < 1) || (rlyno > TUNER_MAX_RELAYS))
  {
    console_println("Invalid relay #");
    return 1;
  }
  RelayModule *rm = &relays[rlyno-1];
  if (!rm->isValidModule())
  {
    console_println("Invalid relay #");
    return 1;
  }  
  rm->setCurrentValue(rlyval,method);
  val = rm->getCurrentValue();
  console_print("Achieved value ");
  console_println(val);
  return 1;
}

int print_tuner_data_cmd(int args, tinycl_parameter *tp, void *v)
{
  console_println("Tuner data:");
  se_print_structure(sizeof(tuner_parameter_fields)/sizeof(tuner_parameter_fields[0]), tuner_parameter_fields, &tpar);
  return 1;
}

void trigger_update(void)
{
  if (!needs_update)
  {
    needs_update = true;
    last_update_tick = millis();
  }
}

int set_tuner_data_cmd(int args, tinycl_parameter *tp, void *v)
{
  char *str = tp[0].ts.str;
  se_set_structure_field(sizeof(tuner_parameter_fields)/sizeof(tuner_parameter_fields[0]), tuner_parameter_fields, &tpar, str);
  se_print_structure(sizeof(tuner_parameter_fields)/sizeof(tuner_parameter_fields[0]), tuner_parameter_fields, &tpar);
  trigger_update();
  return 1;
}

int print_relay_data_cmd(int args, tinycl_parameter *tp, void *v)
{
  int r;
  for (r=0;r<TUNER_MAX_RELAYS;r++)
  {
     RelayModule *rm = &relays[r];
     if (rm->isValidModule())
     {
       console_print("Relay bank ");
       console_println(r+1);
       se_print_structure(sizeof(relay_fields)/sizeof(relay_fields[0]), relay_fields, rm);
       console_println("");
     }
  }
  return 1;
}
int set_relay_data_cmd(int args, tinycl_parameter *tp, void *v)
{
  int rlyno = tp[0].ti.i;
  char *str = tp[1].ts.str;
  if ((rlyno < 1) || (rlyno > TUNER_MAX_RELAYS))
  {
    console_println("Invalid relay #");
    return 1;
  }
  RelayModule *rm = &relays[rlyno-1];
  if (!rm->isValidModule())
  {
    console_println("Invalid relay #");
    return 1;
  }  
  console_print("Setting relay #");
  console_print(rlyno);
  console_print(" ");
  console_println(str);
  se_set_structure_field(sizeof(relay_fields)/sizeof(relay_fields[0]), relay_fields, rm, str);
  se_print_structure(sizeof(relay_fields)/sizeof(relay_fields[0]), relay_fields, rm);
  trigger_update();
  return 1;
}

int rlydef_cmd(int args, tinycl_parameter *tp, void *v)
{
  int rlyno = tp[0].ti.i;
  int rlydef = tp[1].ti.i;
  console_print("Setting relay #");
  console_print(rlyno);
  console_print(" to default # ");
  console_println(rlydef);
  int val;
  if ((rlyno < 1) || (rlyno > TUNER_MAX_RELAYS))
  {
    console_println("Invalid relay #");
    return 1;
  }
  if ((rlydef < 1) || (rlydef > RELAY_DEFAULT_STRUCTS_NUM))
  {
    console_println("Invalid default #");
    return 1;
  }
  RelayModule *rm = &relays[rlyno-1];
  rm->setup(*relay_default_structs[rlydef-1]);
  console_println("New default set");
  return 1;
}

int clear_cache_cmd(int args, tinycl_parameter *tp, void *v)
{ 
  initialize_tuner_cache_entries();
  console_println("Tuner cache cleared");
  return 1;
}

int show_cache_cmd(int args, tinycl_parameter *tp, void *v)
{ 
  int i,p;
  char s[80];
  console_println("Tuner cache contents:");
  for (i=0;i<TUNER_CACHE_ENTRIES;i++)
  { 
    tuner_cache_entry *t = &tce[i];
    if (t->frequency_khz > 0)
    {
      char s[80];
      mini_snprintf(s,sizeof(s)-1,"%03u %05u ",i+1,t->frequency_khz);
      console_print(s);
      for (p=0;p<TUNER_CACHE_NPARMS;p++)
      {
         mini_snprintf(s,sizeof(s)-1," %05u%c%c",t->parm[p],t->switch_state & (1<<(p*2)) ? '+' : '-',t->switch_state & (1<<(p*2+1)) ? '+' : '-');
         console_print(s);
      }
      console_println("");
    }
  }
  return 1;
}

void updateSWRState(swr_state *state, float freq)
{
  state->fwd = swrMeter.fwdPower();
  state->rev = swrMeter.revPower();
  state->cur = swrMeter.curPower();
  state->swr = swrMeter.SWR();
  state->refAngle = RAD2DEG(swrMeter.reflectionPhase());
  state->curAngle = RAD2DEG(swrMeter.currentPhase());
  state->refCoef = swrMeter.reflectionCoefficient();
  state->impedance = swrMeter.calculateImpedance();
  if (freq > 0.0f) state->last_frequency = freq;
}

void printSWRState(swr_state *state)
{
  char s[100];
  mini_snprintf(s,sizeof(s)-1,"Frequency = %f",float2int32(state->last_frequency));
  console_println(s);
  mini_snprintf(s,sizeof(s)-1,"Fwd power = %04f  Rev power = %04f  Cur Power = %04f",float2int32(adjust_pwr(state->fwd)),float2int32(adjust_pwr(state->rev)),float2int32(state->cur));
  console_println(s);
  mini_snprintf(s,sizeof(s)-1,"Ref Angle = %04f  Cur Angle = %04f  SWR = %02f",float2int32(state->refAngle),float2int32(state->curAngle),float2int32(state->swr));
  console_println(s);
  mini_snprintf(s,sizeof(s)-1,"Impedance = %04f + j%04f   Ref = %04f + j %04f",float2int32(state->impedance.re()),float2int32(state->impedance.im()),float2int32(state->refCoef.re()),float2int32(state->refCoef.im()));
  console_println(s);
}

tunerr_condition minimize_swr_step(RelayModule *r, int relstep, float &currentRef, int &currentValue)
{
  int dir;
  int stepsize = (r->getMaxValue() - r->getMinValue()) >> relstep;
  currentValue = r->getCurrentValue();
  swrMeter.sampleSWR();
  if (check_for_rig_tune_abort()) return TUNERR_ABORT;
  currentRef = swrMeter.revPower() / swrMeter.fwdPower();
  for (dir=1;dir>=-1;dir-=2)
  {
    int nextval;
    nextval = currentValue;
    for (;;)
    {
       nextval += stepsize * dir;
       int lastval = r->getCurrentValue();
       r->setCurrentValue(nextval,dir < 0 ? 1 : 2);
       if (r->getCurrentValue() == lastval) break;
       delay(r->getRelaySettleTime());
       swrMeter.sampleSWR();
       if (check_for_rig_tune_abort()) return TUNERR_ABORT;
       float fwd = swrMeter.fwdPower();
       float rev = swrMeter.revPower();
       float testRef = rev/fwd;
       float adjfwd = adjust_pwr(fwd);
       if (adjfwd < tpar.tune_min_power) return TUNERR_POWERLOSS;
       if (adjfwd > tpar.tune_max_power) return TUNERR_POWERHIGH;
       DEBUGMSG("stepsize=%d dir=%d currentValue=%d nextval=%d actval=%d ref=%04f cref=%04f",stepsize,dir,currentValue,nextval,r->getCurrentValue(),float2int32(testRef),float2int32(currentRef));
       nextval = r->getCurrentValue();
       if (testRef < currentRef)
       { 
          currentRef = testRef;
          currentValue = nextval;
       } else 
       {
         if (testRef > (currentRef*tpar.tune_search_relaxation)) break;
       }
    }
  }
  r->setCurrentValue(currentValue);
  delay(r->getRelaySettleTime());
  return TUNERR_SUCCESS;
}

void tuner_set_switches(uint8_t *u)
{
  int i;
  for (i=0;i<(TUNE_SWITCHSTATE_PER_STATE*3);i+=3)
  {
     int r = u[i];
     int s = u[i+1];
     if ((r<1) || (r>TUNER_MAX_RELAYS)) continue;
     if ((s<1) || (s>2)) continue;
     RelayModule *rc = &relays[r-1];
     rc->setSwitchState(s-1,u[i+2] != 0 ? true : false);
     delay(rc->getRelaySettleTime());
  }
}

void tuner_zero_adjustable_relays(void)
{
   for (int r=0;r<TUNER_MAX_RELAYS;r++) 
   {
      RelayModule *rc = &relays[r];
      if (rc->getAutoTune()) rc->setCurrentValue(0);
   }      
}

void tuner_set_bypass(void)
{
  tuner_zero_adjustable_relays();
  tuner_set_switches(tpar.tune_switchstate_bypass);
  tuner_bypass_mode = true;
}

tunerr_condition exhaustive_tune(bool withoutdefault)
{
  int s,n,r;
  float currentRef;
  for (s=withoutdefault ? 1 : 0;s<7;s++)
  {
    switch (s)
    {
      case 1:  if (tpar.tune_switchstate_1[0]==0) continue;
               tuner_set_switches(tpar.tune_switchstate_1);
               break;
      case 2:  if (tpar.tune_switchstate_2[0]==0) continue;
               tuner_set_switches(tpar.tune_switchstate_2);
               break;
      case 3:  if (tpar.tune_switchstate_3[0]==0) continue;
               tuner_set_switches(tpar.tune_switchstate_3);
               break;
      case 4:  if (tpar.tune_switchstate_4[0]==0) continue;
               tuner_set_switches(tpar.tune_switchstate_4);
               break;           
      case 5:  if (tpar.tune_switchstate_5[0]==0) continue;
               tuner_set_switches(tpar.tune_switchstate_5);
               break;           
      case 6:  if (tpar.tune_switchstate_6[0]==0) continue;
               tuner_set_switches(tpar.tune_switchstate_6);
               break;           
    }
    if (s > 0) tuner_zero_adjustable_relays();
    for (n=2;n<9;n++)
    {
      bool improved;
      do
      {
        improved = false;
        for (int r=0;r<TUNER_MAX_RELAYS;r++)
        {
          RelayModule *rc = &relays[r];
          if (!rc->getAutoTune()) continue;
          DEBUGMSG("pass=%d step=%d relay=%d",s,n,r);
          int val = rc->getCurrentValue();
          int currentval;
          tunerr_condition err = minimize_swr_step(rc,n,currentRef,currentval);
          if (err != TUNERR_SUCCESS) return err;
          if (val != rc->getCurrentValue())
              improved = true;
          if (currentRef < tpar.tune_max_ref)
              return TUNERR_SUCCESS;
        }
      } while (improved);
      DEBUGMSG("pass=%d capacitor Inductance=%d nH capacitance=%d pF",s,relays[0].getCurrentValue(),relays[1].getCurrentValue());
    }
  } 
  return TUNERR_HIGHSWR;
}

int tuner_search_cache(uint16_t entry_hz, uint16_t width)
{
  int i;
  uint16_t minfreq = entry_hz - width;
  uint16_t maxfreq = entry_hz + width;
  for (i=0;i<TUNER_CACHE_ENTRIES;i++)
     if ((tce[i].frequency_khz >= minfreq) && (tce[i].frequency_khz <= maxfreq))
      { 
        return i;
      }
  return -1;
}

int tuner_cache_move_to_top(uint16_t entry_hz)
{
  int n;
  int nent = tuner_search_cache(entry_hz,tpar.tune_search_khz_spacing);
  if (nent < 0) return -1;
  tuner_cache_entry temp = tce[nent];
  for (n = nent;n>0;n--)
     tce[n] = tce[n-1];
  tce[0] = temp;
  return nent;
}

int tuner_update_cache(uint16_t entry_hz, uint16_t parms[], uint16_t switch_state)
{
  if (tuner_cache_move_to_top(entry_hz) < 0)
  {
    for (int n = TUNER_CACHE_ENTRIES-1;n>0;n--)
      tce[n] = tce[n-1];
  }
  tce[0].frequency_khz = entry_hz;
  tce[0].switch_state = switch_state;
  for (int n=0;n<TUNER_CACHE_NPARMS;n++)
      tce[0].parm[n] = parms[n];
  trigger_update();
  return 0;
}

int tuner_update_current_state(uint16_t freqkhz)
{
  int p;
  uint16_t switch_state = 0;
  uint16_t parm[TUNER_CACHE_NPARMS];
  for (p=0;p<TUNER_CACHE_NPARMS;p++)
  {
    RelayModule *r = &relays[p];
    if (r->isValidModule())
    {
      parm[p] = r->getCurrentValue();
      switch_state |= r->getSwitchState(0) ? (1<<(2*p)) : 0;
      switch_state |= r->getSwitchState(1) ? (1<<(2*p+1)) : 0;
    } else
      parm[p] = 0;
  }
  return tuner_update_cache(freqkhz, parm, switch_state);
}
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
void loop() {
  if (tinycl_task(sizeof(tcmds) / sizeof(tinycl_command), tcmds, NULL))
  {
    tinycl_do_echo = 1;
    console_print("> ");
  }
  tuner_task();
  save_state_task();
#ifdef TUNER_USER_INTERFACE
  interface_task();
#endif
#ifdef TUNER_REMOTE_WIRELESS
  remote_task();
#endif
}

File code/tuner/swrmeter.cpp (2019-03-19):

/*  SWR Meter Class */

/*
 * Copyright (c) 2018 Daniel Marks

This software is provided 'as-is', without any express or implied
warranty. In no event will the authors be held liable for any damages
arising from the use of this software.

Permission is granted to anyone to use this software for any purpose,
including commercial applications, and to alter it and redistribute it
freely, subject to the following restrictions:

1. The origin of this software must not be misrepresented; you must not
   claim that you wrote the original software. If you use this software
   in a product, an acknowledgment in the product documentation would be
   appreciated but is not required.
2. Altered source versions must be plainly marked as such, and must not be
   misrepresented as being the original software.
3. This notice may not be removed or altered from any source distribution.
 */


#include "Arduino.h"
#include "swrmeter.h"
#include "debugmsg.h"


#define FULL_SCALE_AD_VOLTS 3.3f
#define FULL_SCALE_AD_COUNTS 4096.0f
#define VOLTS_TO_COUNTS (FULL_SCALE_AD_COUNTS/FULL_SCALE_AD_VOLTS)
#define LOAD_RESISTOR     10000.0f
#define SERIES_RESISTANCE 1000.0f
#define SCALEVAL_DEFAULT (((SERIES_RESISTANCE+LOAD_RESISTOR)/LOAD_RESISTOR)/VOLTS_TO_COUNTS)
#define OFFSET_DEFAULT 0.0f

#define NUMBER_SWR_SAMPLES 11

void quicksort(unsigned short list[],int m,int n)
{
    unsigned short temp;
    int key,i,j,k;
    if( m < n)
    {
        k = ((m+n)/2);
        temp = list[m]; list[m] = list[k];list[k] = temp;
        key = list[m];
        i = m+1;
        j = n;
        while(i <= j)
        {
            while((i <= n) && (list[i] <= key))
                i++;
            while((j >= m) && (list[j] > key))
                j--;
            if( i < j)
            {
                temp = list[i]; list[i] = list[j];list[j] = temp;
            }
        }
        temp = list[m]; list[m] = list[j];list[j] = temp;
 
        quicksort(list,m,j-1);
        quicksort(list,j+1,n);
    }
}

unsigned short analogReadCollect(byte pin, int nsamp)
{
  unsigned short samps[nsamp];
#if 1
  adc_dev *dev = PIN_MAP[pin].adc_device;
  int pinMap = PIN_MAP[pin].adc_channel;
  adc_set_sample_rate(dev, ADC_SMPR_55_5); /* ADC_SMPR_13_5 */
  adc_reg_map *regs = dev->regs;
  adc_set_reg_seqlen(dev, 1);
  regs->SQR3 = pinMap;

  for (uint16_t j = 0; j < nsamp; j++ )
  {
    regs->CR2 |= ADC_CR2_SWSTART;
    while (!(regs->SR & ADC_SR_EOC))
        ;
    samps[j]=(regs->DR & ADC_DR_DATA);
  }
#else
  for (int i=0;i<nsamp;i++) samps[i] = analogRead(pin);
#endif
  quicksort(samps,0,nsamp-1);
  return samps[nsamp/2]; 
}

void swr_calib_parms_default(swr_calib_parms *p)
{
  p->offset = OFFSET_DEFAULT;
  p->scale = SCALEVAL_DEFAULT;
  //p->logoffset = LOGOFFSET_DEFAULT;
  //p->logscale = LOGSCALE_DEFAULT; 
}

void SWRMeter::setup(void)
{
  // set all of the pins to be analog
    pinMode(SWRMETER_ANALOG_FWDPWR, INPUT_ANALOG);
    pinMode(SWRMETER_ANALOG_REVPWR, INPUT_ANALOG);
    pinMode(SWRMETER_ANALOG_CURPWR, INPUT_ANALOG);
    pinMode(SWRMETER_ANALOG_DUTYCYCLEFWD, INPUT_ANALOG);
    pinMode(SWRMETER_ANALOG_DUTYCYCLEREV, INPUT_ANALOG);
    pinMode(SWRMETER_ANALOG_DUTYCYCLECUR, INPUT_ANALOG);
    pinMode(SWRMETER_ANALOG_CURDELAYPHASE, INPUT_ANALOG);
    pinMode(SWRMETER_ANALOG_CURPHASE, INPUT_ANALOG);
    pinMode(SWRMETER_ANALOG_REVPHASE, INPUT_ANALOG);
    pinMode(SWRMETER_ANALOG_REVDELAYPHASE, INPUT_ANALOG);
    pinMode(SWRMETER_SAMPLE_LEVEL_IO, OUTPUT);

    digitalWrite(SWRMETER_SAMPLE_LEVEL_IO, HIGH);
    delayMicroseconds(100);
    sampleMAXVOLTAGELEVEL = analogReadCollect(SWRMETER_ANALOG_DUTYCYCLEFWD,NUMBER_SWR_SAMPLES);
    digitalWrite(SWRMETER_SAMPLE_LEVEL_IO, LOW);
}

void SWRMeter::sampleSWR(void)
{
  sampleFWDPWR = analogReadCollect(SWRMETER_ANALOG_FWDPWR,NUMBER_SWR_SAMPLES);
  sampleREVPWR = analogReadCollect(SWRMETER_ANALOG_REVPWR,NUMBER_SWR_SAMPLES);
  sampleCURPWR = analogReadCollect(SWRMETER_ANALOG_CURPWR,NUMBER_SWR_SAMPLES);
  sampleDUTYCYCLEFWD = analogReadCollect(SWRMETER_ANALOG_DUTYCYCLEFWD,NUMBER_SWR_SAMPLES);
  sampleDUTYCYCLEREV = analogReadCollect(SWRMETER_ANALOG_DUTYCYCLEREV,NUMBER_SWR_SAMPLES);
  sampleDUTYCYCLECUR = analogReadCollect(SWRMETER_ANALOG_DUTYCYCLECUR,NUMBER_SWR_SAMPLES);
  sampleCURDELAYPHASE = analogReadCollect(SWRMETER_ANALOG_CURDELAYPHASE,NUMBER_SWR_SAMPLES);
  sampleCURPHASE = analogReadCollect(SWRMETER_ANALOG_CURPHASE,NUMBER_SWR_SAMPLES);
  sampleREVPHASE = analogReadCollect(SWRMETER_ANALOG_REVPHASE,NUMBER_SWR_SAMPLES);
  sampleREVDELAYPHASE = analogReadCollect(SWRMETER_ANALOG_REVDELAYPHASE,NUMBER_SWR_SAMPLES);
}

void SWRMeter::setImpedance(float pZ0)
{
	Z0 = pZ0;
}

float calculatePower(unsigned short samples, swr_calib_parms &p)
{
	float pwr = samples;
  pwr = p.offset + pwr*p.scale;
  //pwr = p.offset + pwr*p.scale + p.logscale*logf(p.logoffset*pwr + 1.0f);
	return pwr < 1.0e-6f ? 1.0e-6f : pwr;
}

float SWRMeter::fwdPower(void)
{
	return calculatePower(sampleFWDPWR,swrcalib.fwdParms);
}

float SWRMeter::revPower(void)
{
	return calculatePower(sampleREVPWR,swrcalib.revParms);
}

float SWRMeter::curPower(void)
{
  return calculatePower(sampleCURPWR,swrcalib.curParms);
}

float SWRMeter::magReflection(void)
{
  return revPower() / fwdPower();
}

float SWRMeter::SWR(void)
{
	float magRef = magReflection();
	return (1.0f+magRef)/(1.0f-magRef);
}

float SWRMeter::reflectionPhase(void)
{
  float phaseReflection = FM_PI*((float)sampleREVPHASE)/((float)sampleMAXVOLTAGELEVEL);
  if (sampleREVDELAYPHASE < sampleREVPHASE)
    phaseReflection = -phaseReflection;
  return phaseReflection;
}

float SWRMeter::currentPhase(void)
{
  float phaseCur = FM_PI*((float)sampleCURPHASE)/((float)sampleMAXVOLTAGELEVEL);
  if (sampleCURDELAYPHASE < sampleCURPHASE)
    phaseCur = -phaseCur;
  return phaseCur;
}

Complex SWRMeter::reflectionCoefficient(void)
{
  float magRef = magReflection();
  float phaseReflection = reflectionPhase();

  return Complex(magRef*cosf(phaseReflection),magRef*sinf(phaseReflection));
}

Complex SWRMeter::calculateImpedance(void)
{
	Complex ref = reflectionCoefficient();
	return ((Complex(1.0f,0.0f)+ref)/(Complex(1.0f,0.0f)-ref))*Z0;
}

Complex SWRMeter::currentCoefficient(void)
{
  float magCur = curPower() / fwdPower();
  float phaseCur = currentPhase();

  return Complex(magCur*cosf(phaseCur),magCur*sinf(phaseCur));
}
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

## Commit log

2018-08-24 added Bill of Materials
    [Controller.ods, Remote.ods, Remote.sch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]
2018-09-01 Added separate relay and relay control board
    [RelayControl-B.Cu.gbr, RelayControl-B.Mask.gbr, RelayControl-B.SilkS.gbr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]
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2018-09-03 Added RF Shielding to ReversibleSection
    [Relays-B.Cu.gbr, Relays-B.Mask.gbr, Relays-B.SilkS.gbr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]
2018-09-03 A few more vias on the ReversibleSection
    [TunerSection-B.Cu.gbr, TunerSection-B.Mask.gbr, TunerSection-B.SilkS.gbr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]
2018-09-10 Modified RelayControl and Reversible Section to Isolate Digital from Analog sections using RF chokes
    [RelayControl-B.Cu.gbr, RelayControl-B.Mask.gbr, RelayControl-B.SilkS.gbr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]
2018-09-11 Added extra filtering and shunt to RF ground
    [RelayControl-B.Cu.gbr, RelayControl-B.Mask.gbr, RelayControl-B.SilkS.gbr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]
2018-09-15 JLCPCB submitted RelayControl version
    [RelayControl-B.Cu.gbr, RelayControl-B.Mask.gbr, RelayControl-B.SilkS.gbr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]
2018-09-23 JLCPCB order 09232018 - improved grounding - improved I2C cabling - NEO7M port - support for common mode chokes - relay board now has capacitors on all coils
    [Controller-B.Cu.gbr, Controller-B.Mask.gbr, Controller-B.SilkS.gbr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]
2018-10-07 Relay boards changed to have coil terminals all on same side
    [Controller.kicad_pcb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]
2018-10-22 Added boards for SMIH/Schrack Relays
    [Controller-B.Cu.gbr, Controller-B.Mask.gbr, Controller-B.SilkS.gbr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]
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2018-10-24 Error in pinout HK19F fixed
    [Relays-B.Cu.gbr, Relays-B.Mask.gbr, Relays-B.SilkS.gbr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]
2018-11-01 JLCPCB Nov 1 2018
    [Relays-B.Cu.gbr, Relays-B.Mask.gbr, Relays-B.SilkS.gbr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]
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2018-12-20 Got rid of two non-working boards
    [Relays-B.Cu.gbr, Relays-B.Mask.gbr, Relays-B.SilkS.gbr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]
2019-02-16 Moved some grounds around
    [Controller-B.Cu.gbr, Controller-B.Mask.gbr, Controller-B.SilkS.gbr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]
2019-02-18 Tandem Match PCB added
    [Controller.kicad_pcb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]
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2019-02-21 Fixed TandemMatch grounding problem
    [Controller-B.Cu.gbr, Controller-B.Mask.gbr, Controller-B.SilkS.gbr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]
2019-02-24 Added new DelayLine board, modified TandemMatch
    [DelayLine-B.Cu.gbr, DelayLine-B.Mask.gbr, DelayLine-B.SilkS.gbr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]
2019-02-24 Added phase reversal transformer
    [DelayLine-B.Cu.gbr, DelayLine-B.Mask.gbr, DelayLine-B.SilkS.gbr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]
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2019-02-24 Modified DelayLine to include bypass control
    [DelayLine-B.Cu.gbr, DelayLine-B.Mask.gbr, DelayLine-B.SilkS.gbr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]
2019-02-25 Changed DelayLine to short out sections
    [DelayLine-B.Cu.gbr, DelayLine-B.Mask.gbr, DelayLine-B.SilkS.gbr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]
2019-02-25 Stupid mistake, went to another method
    [DelayLine-B.Cu.gbr, DelayLine-B.Mask.gbr, DelayLine-B.SilkS.gbr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]
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2019-02-27 Added more instrumentation to TandemMatch, fixed grounding issue
    [DelayLine-B.Cu.gbr, DelayLine-B.Mask.gbr, DelayLine-B.SilkS.gbr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]
2019-03-02 Removed 1k resistors, did some more rearranging on TandemMatch
    [Controller-B.Cu.gbr, Controller-B.Mask.gbr, Controller-B.SilkS.gbr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]
2019-03-03 Added BNC and screw terminal combo pads
    [Controller-B.Cu.gbr, Controller-B.Mask.gbr, Controller-B.SilkS.gbr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]
2019-03-04 Changed over yet more to BNC
    [DelayLine-B.Cu.gbr, DelayLine-B.Mask.gbr, DelayLine-B.SilkS.gbr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]
2019-03-05 TandenMatch now has DC-RF bias tee
    [LittleDelayLine-B.Cu.gbr, LittleDelayLine-B.Mask.gbr, LittleDelayLine-B.SilkS.gbr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]
2019-03-06 Modified connectors on Reversible boards
    [Controller-B.Cu.gbr, Controller-B.Mask.gbr, Controller-B.SilkS.gbr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]
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2019-03-10 Actually tuning code now!
    [Controller-B.Cu.gbr, Controller-B.Mask.gbr, Controller-B.SilkS.gbr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]
2019-03-12 Put level shifters into controller
    [Controller-B.Cu.gbr, Controller-B.Mask.gbr, Controller-B.SilkS.gbr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]
2019-03-13 Changed bypass method on delay lines
    [Controller-B.Cu.gbr, Controller-B.Mask.gbr, Controller-B.SilkS.gbr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]
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2019-03-17 Changed I2C cable pinoutgit add Tunergit add Tuner Also added ICOM rig support
    [Controller-B.Cu.gbr, Controller-B.Mask.gbr, Controller-B.SilkS.gbr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]
2019-03-19 Fixed icom tuning bad tuning report
    [Controller-B.Cu.gbr, Controller-B.Mask.gbr, Controller-B.SilkS.gbr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]
2019-03-20 Fixed spacing between BNC connectors in Delay Lines
    [DelayLine-B.Cu.gbr, DelayLine-B.Mask.gbr, DelayLine-B.SilkS.gbr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]
2019-03-22 Made PCF8574 LCD adapter with buttons
    [LCDadapter-B.Cu.gbr, LCDadapter-B.Mask.gbr, LCDadapter-B.SilkS.gbr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]
2019-03-23 Added some initial I2C user interface stuff
    [Controller-B.Cu.gbr, Controller-B.Mask.gbr, Controller-B.SilkS.gbr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]
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2019-03-27 Added nonswitched output to ReversibleSections
    [LCDadapter-B.Cu.gbr, LCDadapter-B.Mask.gbr, LCDadapter-B.SilkS.gbr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]
2019-03-30 Change named to DirectionalCoupler, fixed order of two pins in QuadCoupler
    [DirectionalCoupler.kicad_pcb, DirectionalCoupler.sch, QuadCoupler.kicad_pcb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]
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2019-04-08 Added LittleSwitchBus and RelayBreakout
    [LittleSwitchBus-B.Cu.gbr, LittleSwitchBus-B.Mask.gbr, LittleSwitchBus-B.SilkS.gbr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]
2019-04-09 Added Bill of Materials to PCBs
    [Controller.ods, DelayLine.ods, DirectionalCoupler.ods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]
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2019-04-13 Added LEDs to OptoisolatedRelay
    [OptoisolatedRelay-B.Cu.gbr, OptoisolatedRelay-B.Mask.gbr, OptoisolatedRelay-B.SilkS.gbr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]
2019-04-16 Added some fixes to tuner code
    [LittleSwitchBus-B.Cu.gbr, LittleSwitchBus-B.Mask.gbr, LittleSwitchBus-B.SilkS.gbr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]
2019-05-23 Some modifications to Quadcoupler for easier access
    [QuadCoupler-B.Cu.gbr, QuadCoupler-B.Mask.gbr, QuadCoupler-B.SilkS.gbr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]
2019-07-03 Added switchable low pass filter PCB
    [Filter-B.Cu.gbr, Filter-B.Mask.gbr, Filter-B.SilkS.gbr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]
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2019-10-26 Changed the way the tuning is done so that the bypass is automatically selected when zero inductance is needed
    [Controller.ods, Controller.sch]
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2019-11-24 Changed capacitance high-Z low-Z to have less series inductance
    [QROMatch-B.Cu.gbr, QROMatch-B.Mask.gbr, QROMatch-B.SilkS.gbr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]
2019-11-25 Added extra capacitors between relay power and ground posts
    [DelayLine-B.Cu.gbr, DelayLine-B.Mask.gbr, DelayLine-B.SilkS.gbr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]
2019-11-25 Added extra capacitors to ground to large relay boards
    [DelayLine-B.Cu.gbr, DelayLine-B.Mask.gbr, DelayLine-B.SilkS.gbr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]
2019-11-25 Missed the gerbers for DelayLine
    [DelayLine-B.Cu.gbr, DelayLine-B.Mask.gbr, DelayLine-B.SilkS.gbr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]
2019-11-25 Changed some of the capacitors to NC becaue they might cause problems in some situations
    [LittleDelayLine.sch, LittleSwitchBus.sch, TunerSection.sch]
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2019-11-30 Changed from 2x12 IDC to more common 2x13 IDC
    [QROMatch-B.Cu.gbr, QROMatch-B.Mask.gbr, QROMatch-B.SilkS.gbr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]
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
